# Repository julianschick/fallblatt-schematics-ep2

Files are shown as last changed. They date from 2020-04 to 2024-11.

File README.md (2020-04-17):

# Fallblattanzeiger der S-Bahn-Berlin

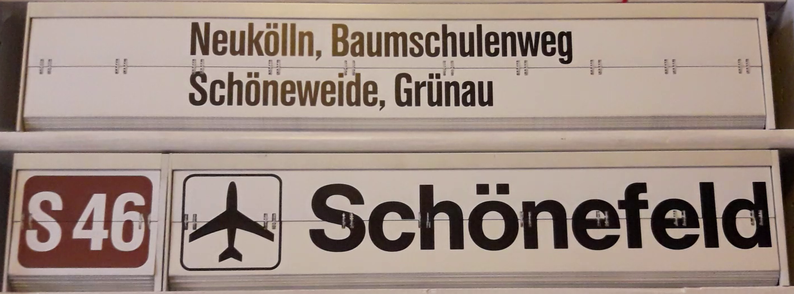
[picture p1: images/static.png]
Ansicht des Anzeigers


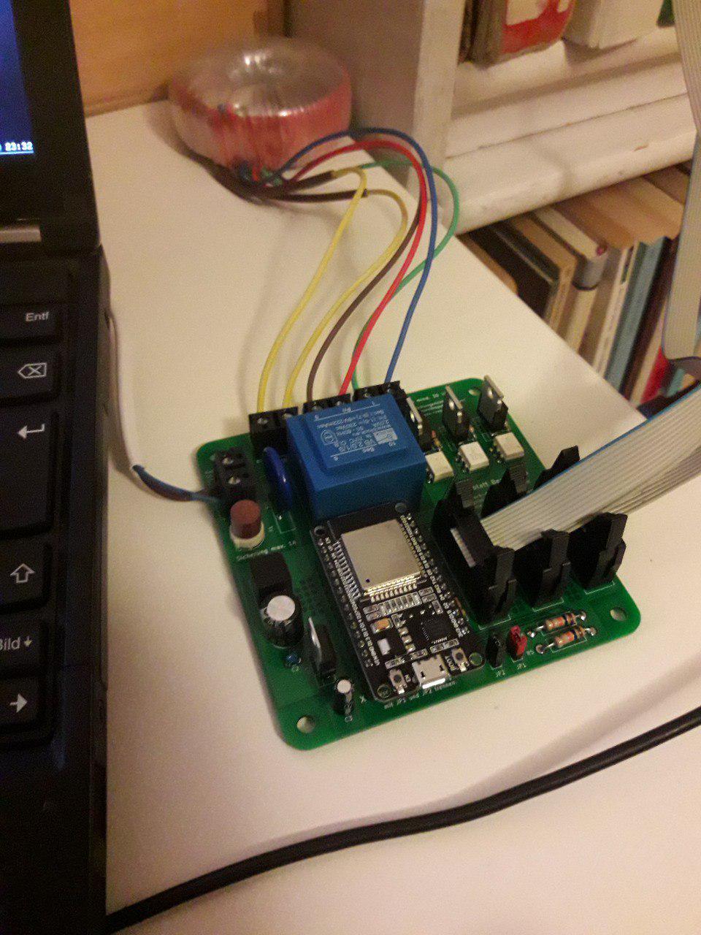
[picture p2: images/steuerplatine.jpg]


Platine zur Ansteuerung von 3 Fallblattmodulen (typischerweise Linie, Fahrtziel und Laufweg) mit einem ESP32-Development-Board. Gedacht für Module der *Epoche 2* (siehe [Wikipedia](https://de.wikipedia.org/wiki/Fallblattanzeige)) und ein Eingriff in die Platine der Module ist erforderlich. Der Synchronmotor wird nicht über die Transistorschaltung auf der Platine des Fallblattmoduls gesteuert. Vielmehr wird die Platine so überbrückt, dass der Microcontroller direkten Zugriff auf die Hall-Sensoren hat und über einen eigenen Triac den Synchronmotor direkt steuert.

Zur Stromversorgung wird die Platine an 230 V Netzspannung angeschlossen. Ein großer Trafo, der nicht auf der Platine verbaut wird, sondern über Schraubklemmen angeschlossen werden kann, spannt auf 48V AC herunter. Damit werden die Synchronmotoren der Module betrieben. Ein weiterer Trafo, der auf der Platine montiert wird, spannt auf 9V AC herunter, die gleichgerichtet und mit einem Linearregler auf Logik-Betriebsspannung 3,3V gebracht werden.

## Modifikationen an der Platine des Fallblattmoduls

Der unveränderte Schaltplan der Platine ist als [KiCad-Schaltplan](images/schaltplan-modul/schaltplan-modul.sch) und [PDF](images/schaltplan-modul.pdf) im Repo abgelegt. Soweit möglich, sind Typenbezeichnung der Bauteile mit angegeben, diese sind allerdings mit Google heute nur schwer zu deuten.

Ähnlich wie bei den modernen Varianten (siehe auch [fallblatt-schematics-ep3](https://github.com/julianschick/fallblatt-schematics-ep3)) der Fallblattmodule sind zwei Sensoren verbaut: Ein Sensor, der jedes fallende Blatt zählt (Flap) und einen, der ein bestimmtes Blatt als Nullstellung markiert (Home). Im Gegensatz zu den moderneren Exemplaren sind das allerdings keine Photodioden sondern Hall-Sensoren, an denen ein Magnet vorbeistreicht. Wenn kein Magnet in der Nähe ist, liegt auf dem Ausgang des Sensors VCC an, kommt der Magnet vorbei, so wird der Ausgang sehr sauber (ohne Gewackel) auf GND gezogen. Im Betrieb mit dem Mikrocontroller habe ich allerdings festgestellt, dass die Flap-Sensoren einerseits gerne etwas zu früh triggern, sodass das Blatt noch klemmt, und andererseits beim erneuten Anlaufen manchmal durch die Induktion des in Bewegung gesetzten Magneten noch einmal kurz getriggert werden. Gelöst habe ich beide Probleme auf Softwareseite durch etwas längeres Weiterlaufen und durch Ignorieren des Flap-Sensors direkt nach dem Anlaufen.

Die folgenden Pläne und Bilder zeigen die notwendigen Modifikationen. Einmal wird Pin 5 des Anschlusssteckers von Pin 10 des Anschlusssteckers getrennt, indem ein Widerstand und eine Diode entfernt werden. Außerdem wird Pin 10 direkt mit dem Flap-Hall-Sensor verbunden, durch setzen einer Brücke auf der Platine, wo schon zwei vorbereitete Pads nebeneinander liegen (violette Brücke). Zuletzt wird der Triac entfernt und überbrückt (blaue Brücke).

**Schaltplan mit Modifikationen**

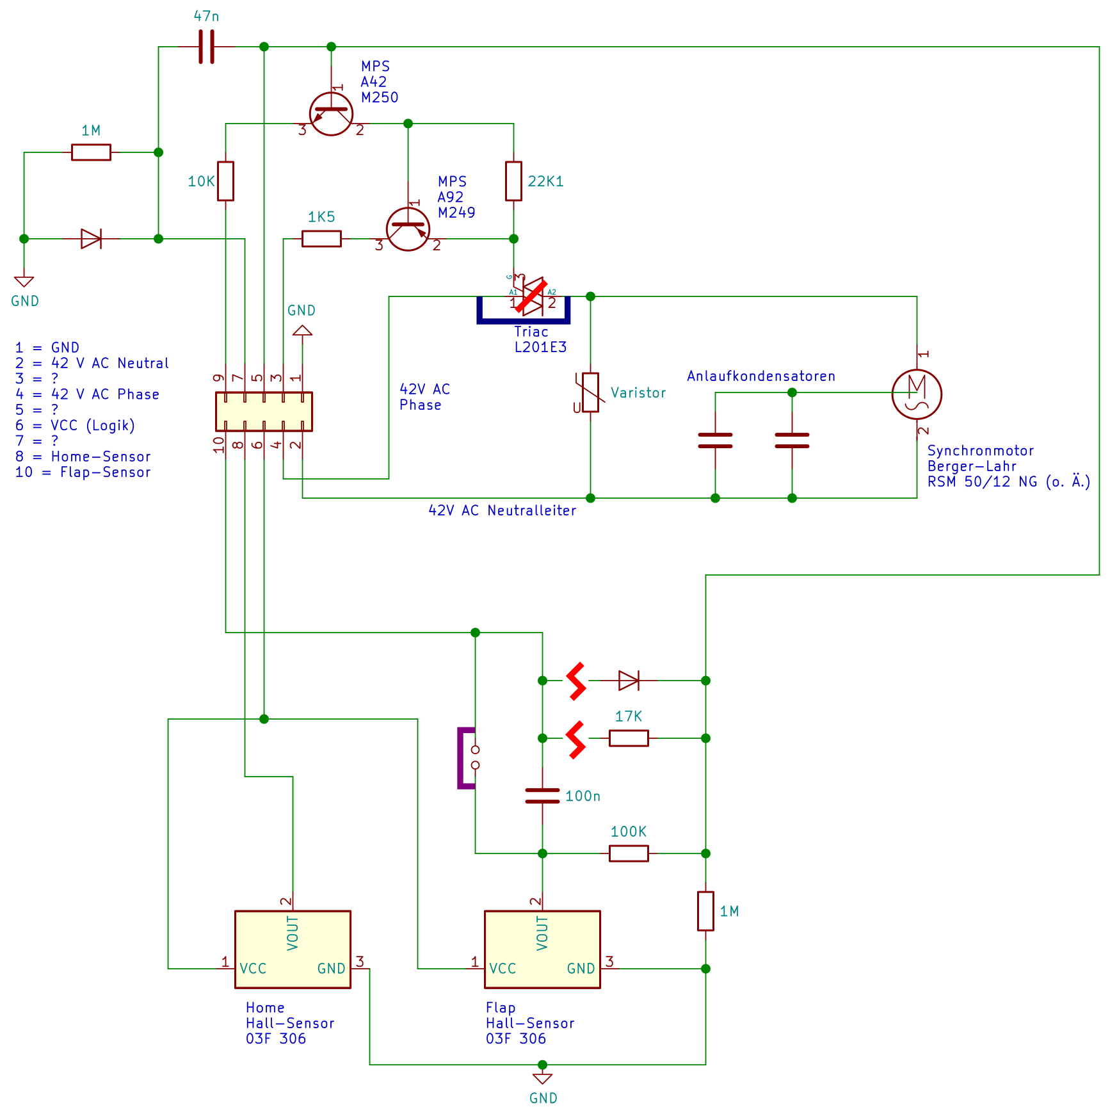
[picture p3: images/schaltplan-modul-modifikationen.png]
Schaltplan mit Modifikationen


Dieses Bild auch als [PDF](images/schaltplan-modul-modifikationen.pdf) und [SVG](images/schaltplan-modul-modifikationen.svg).

**Modifikationen an der Platine** (blaue und violette Brücke, entfernte Teile)

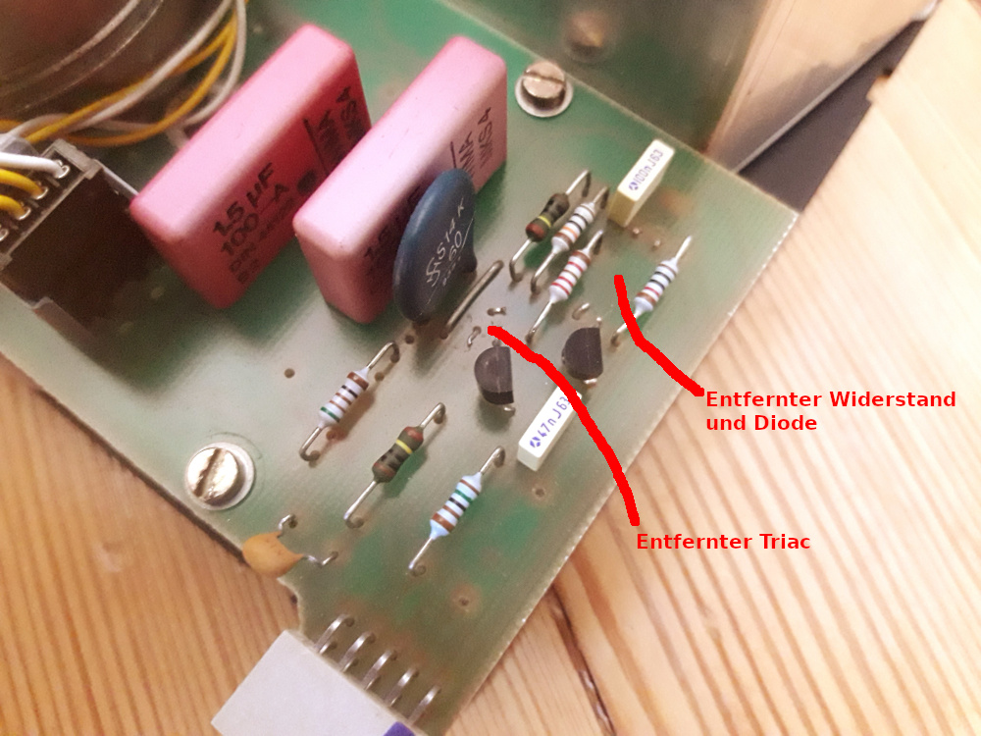
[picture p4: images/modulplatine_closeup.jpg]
Modifikationen an der Platine
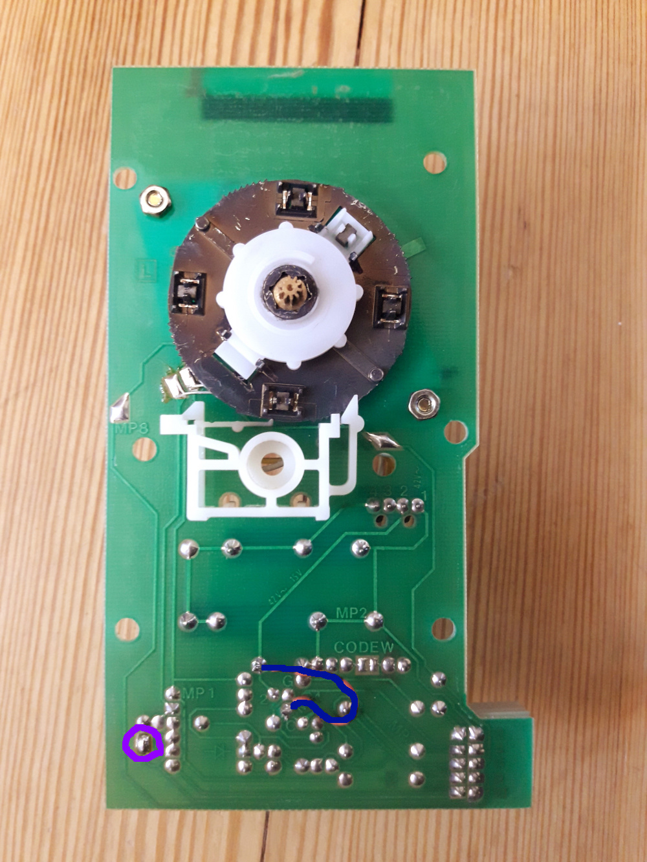
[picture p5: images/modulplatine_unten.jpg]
Modifikationen an der Platine
 

**Gesamte Platine des Fallblattmoduls / Synchronmotor**

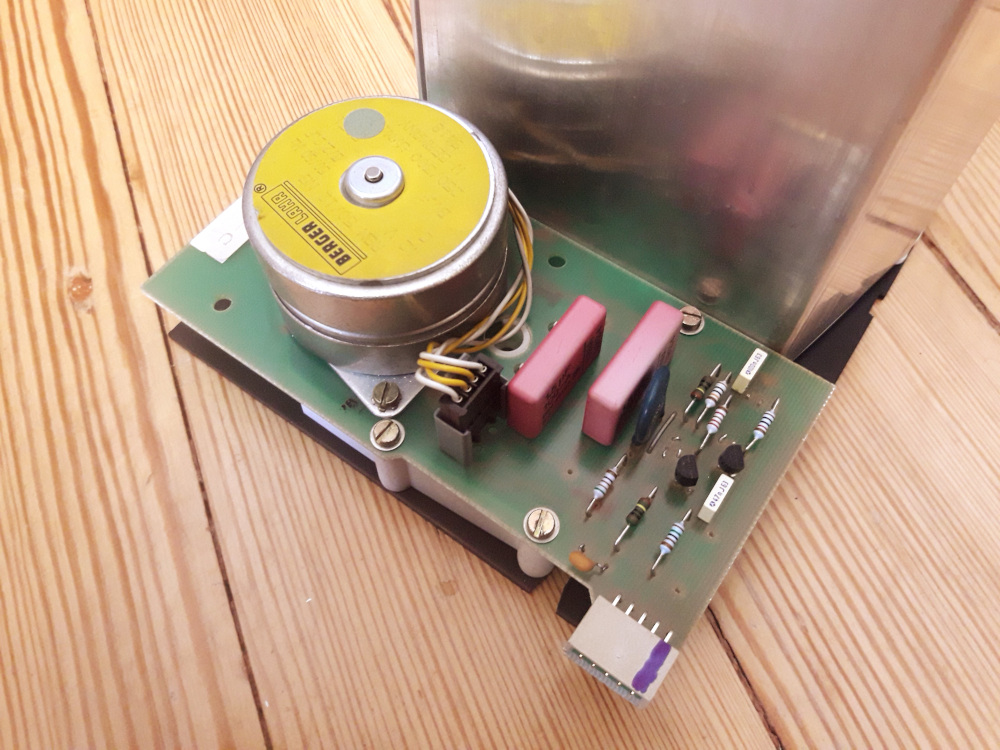
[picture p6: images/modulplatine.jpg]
Modulplatine
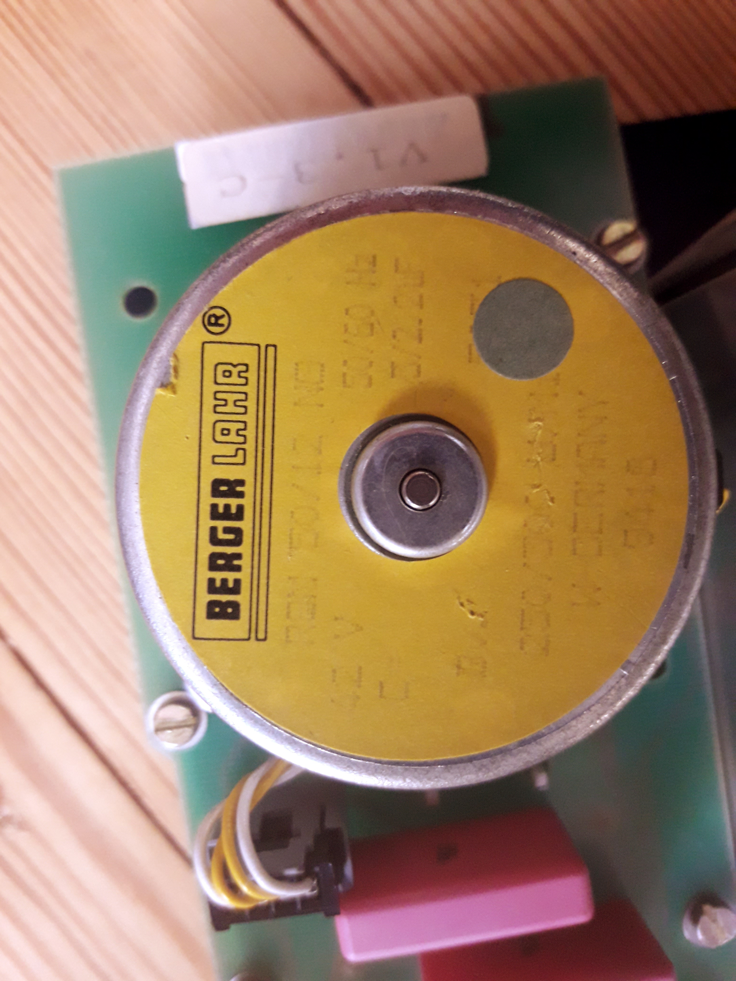
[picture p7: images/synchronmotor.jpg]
Synchronmotor
 

**Polbelegung des Anschlusses**

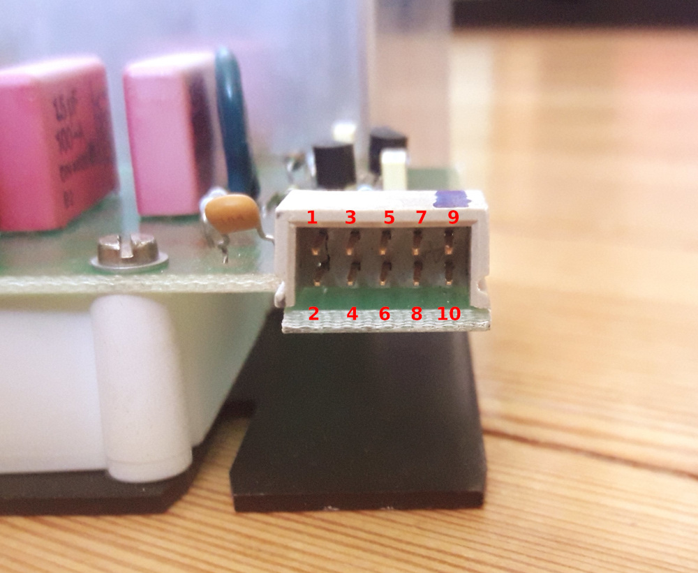
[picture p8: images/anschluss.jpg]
Polbelegung des Anschlusses


## Teileliste

* ESP32-Development-Board (es gibt 2 Varianten bei eBay, für diese Platine wird die üblichere mit 15 Pins je Reihe und GND/VCC  nebeneinander, nicht auf gegenüberliegenden Pins benötigt; diese wird oft unter dem Namen _DEVKITV1_ oder _NodeMCU_ verkauft). Das folgende Pinout ist das korrekte:

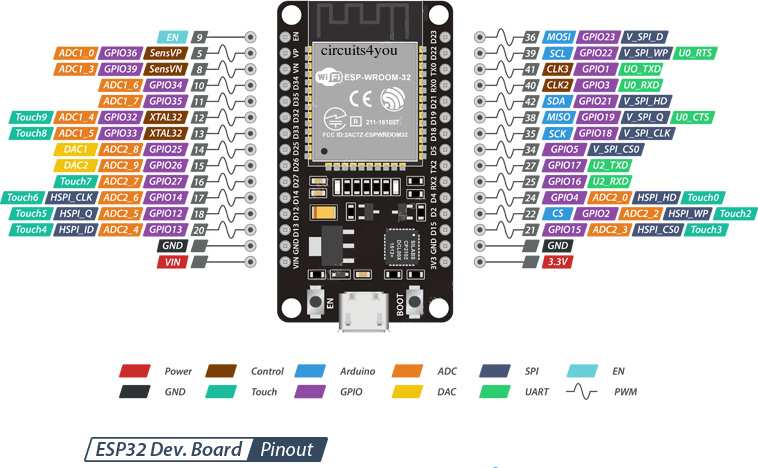
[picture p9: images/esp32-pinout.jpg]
ESP32-Pinout


* Netztrafo 48V (eigentlich 42V) mit Wumms, mind. 200mA pro Modul, der Synchronmotor zieht so viel. Zum Beispiel [der hier](https://www.voelkner.de/products/1011896/TRU-Components-TC-RKT30-2X24-Ringkerntransformator-1-x-230V-2-x-24V-30-VA-625mA.html)
* [Transformator 9V _Block VB 2,0/1/9_](https://www.reichelt.de/printtrafo-2-va-9-v-222-ma-rm-20-mm-ei-30-15-5-109-p27328.html)
* Rundsicherung 1A mit Halter Littelfuse, RM 5mm
* Varistor, mind. 300V, RM 10mm
* [Brückengleichrichter Rund, Wechselstrompins gegenüber, RM 5mm](https://www.reichelt.de/brueckengleichrichter-100-v-1-5-a-b70c1500rund-p181713.html)
* 4 x Schraubklemme 2-polig RM 7,5mm
* [Spannungsregler 3,3V Formfaktor TO-220 _STM LD1117 V33C_](https://www.reichelt.de/ldo-regler-fest-3-3-v-to-220-ld1117-v33c-p200891.html?)
* 3 x Optotriac (Triac mit Optokoppler) MOC3041M, Formfaktor DIP-6
* 3 x Leistungstriac BT136-600, Formfaktor TO-220
* Elektrolytkondensator 470u, RM 5mm
* Elektrolytkondensator 10u, RM 2mm
* Kondensator 100n, RM 2,5mm
* 6 x Widerstand 10K, RM 15mm
* 3 x Widerstand 220, RM 10mm
* 3 x Widerstand 330, RM 10mm
* 2 x Jumpersteckplatz und 2 x Pinheader Female für das ESP32-Board
* 3 x Anschlüsse für die Fallblattmodule (2 x 5 Pole), RM 2,54mm

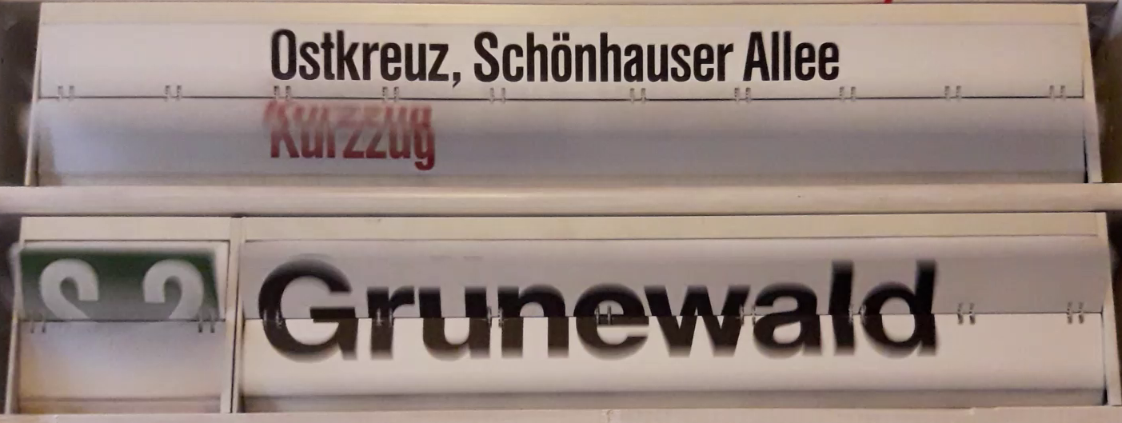
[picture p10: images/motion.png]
In Bewegung


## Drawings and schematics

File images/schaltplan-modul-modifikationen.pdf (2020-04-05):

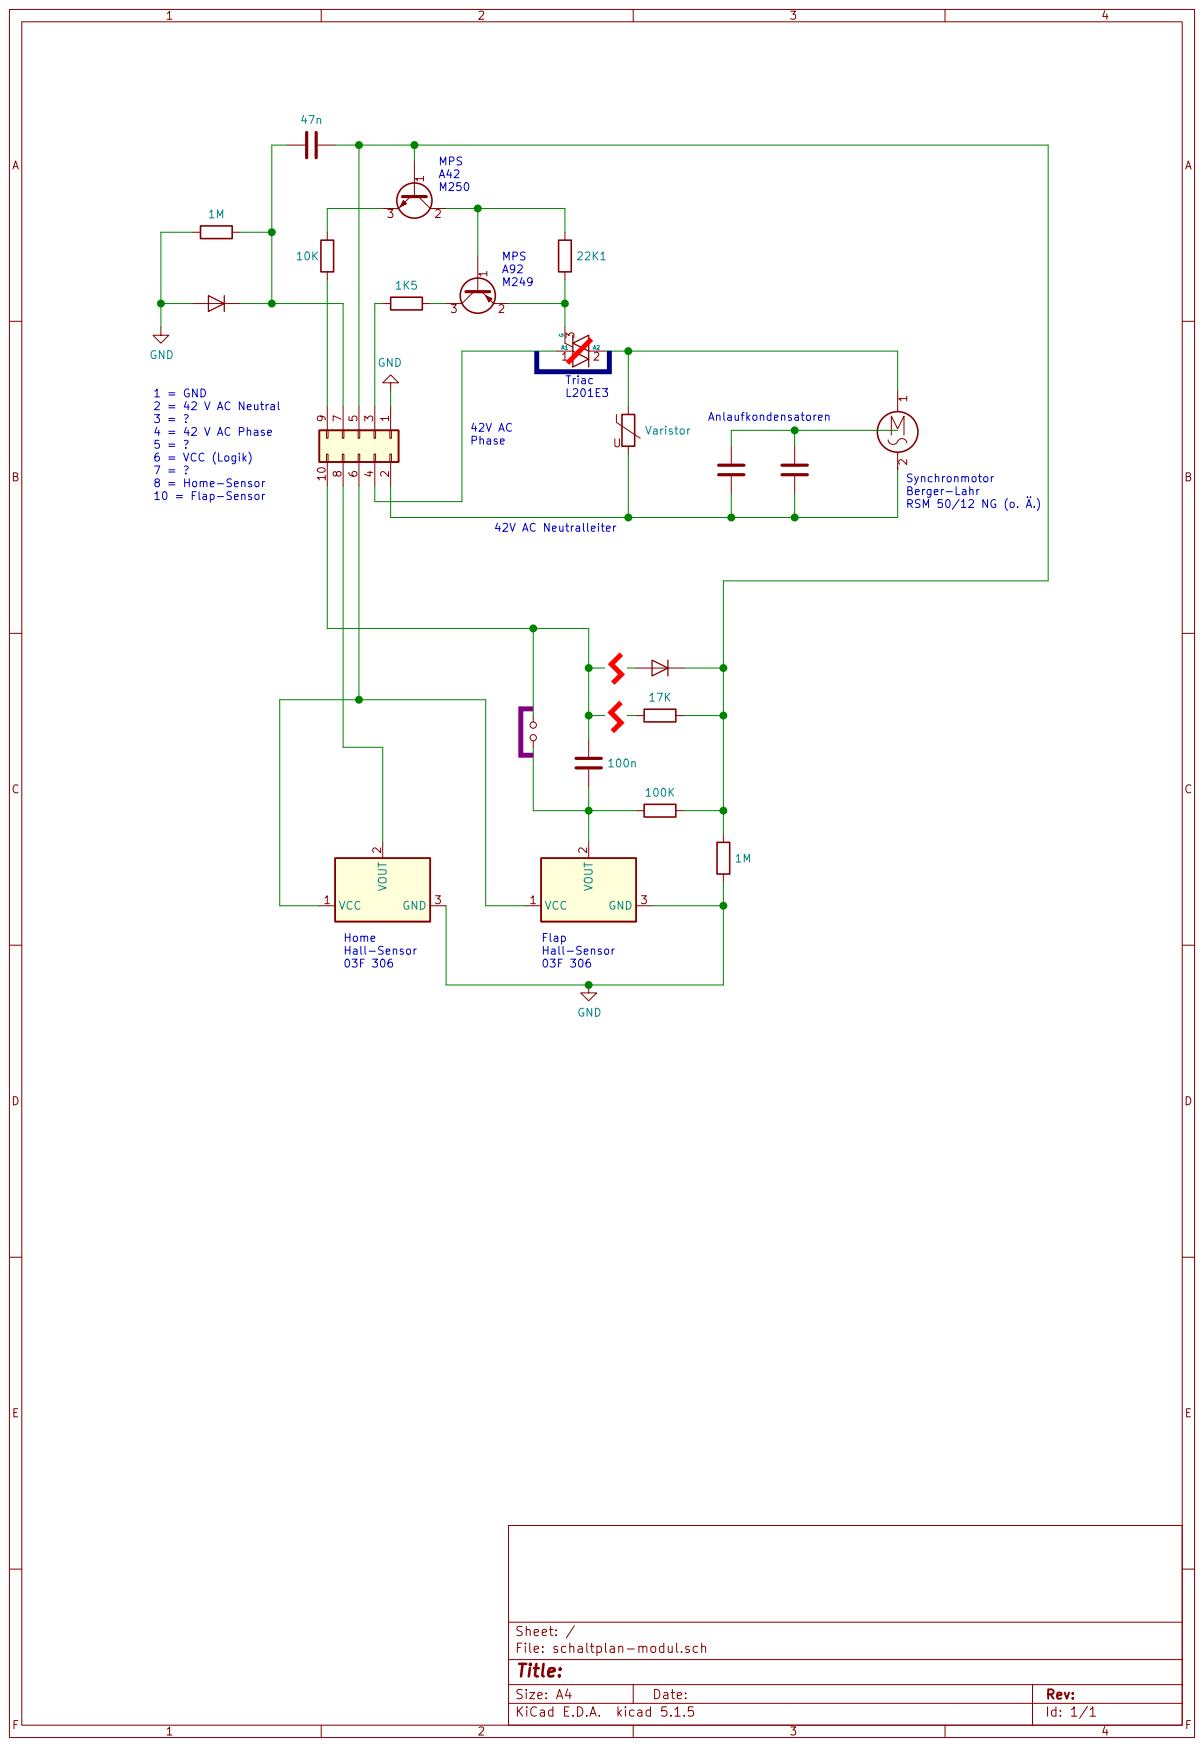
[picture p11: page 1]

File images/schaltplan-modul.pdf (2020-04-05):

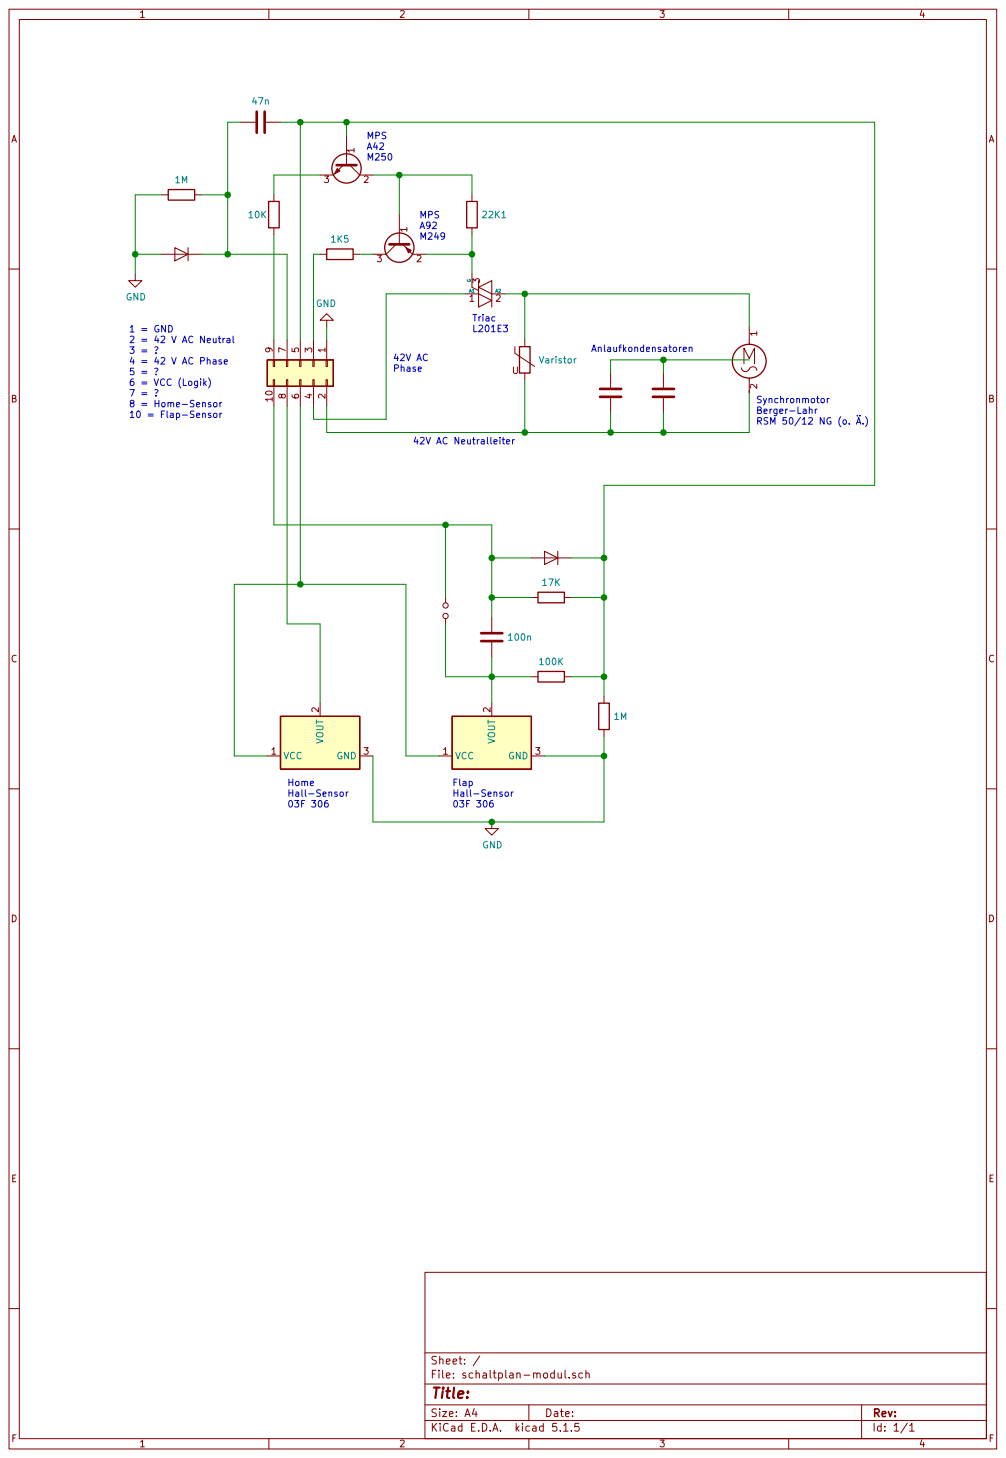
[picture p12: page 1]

File: schaltplan-modul.sch Sheet: /

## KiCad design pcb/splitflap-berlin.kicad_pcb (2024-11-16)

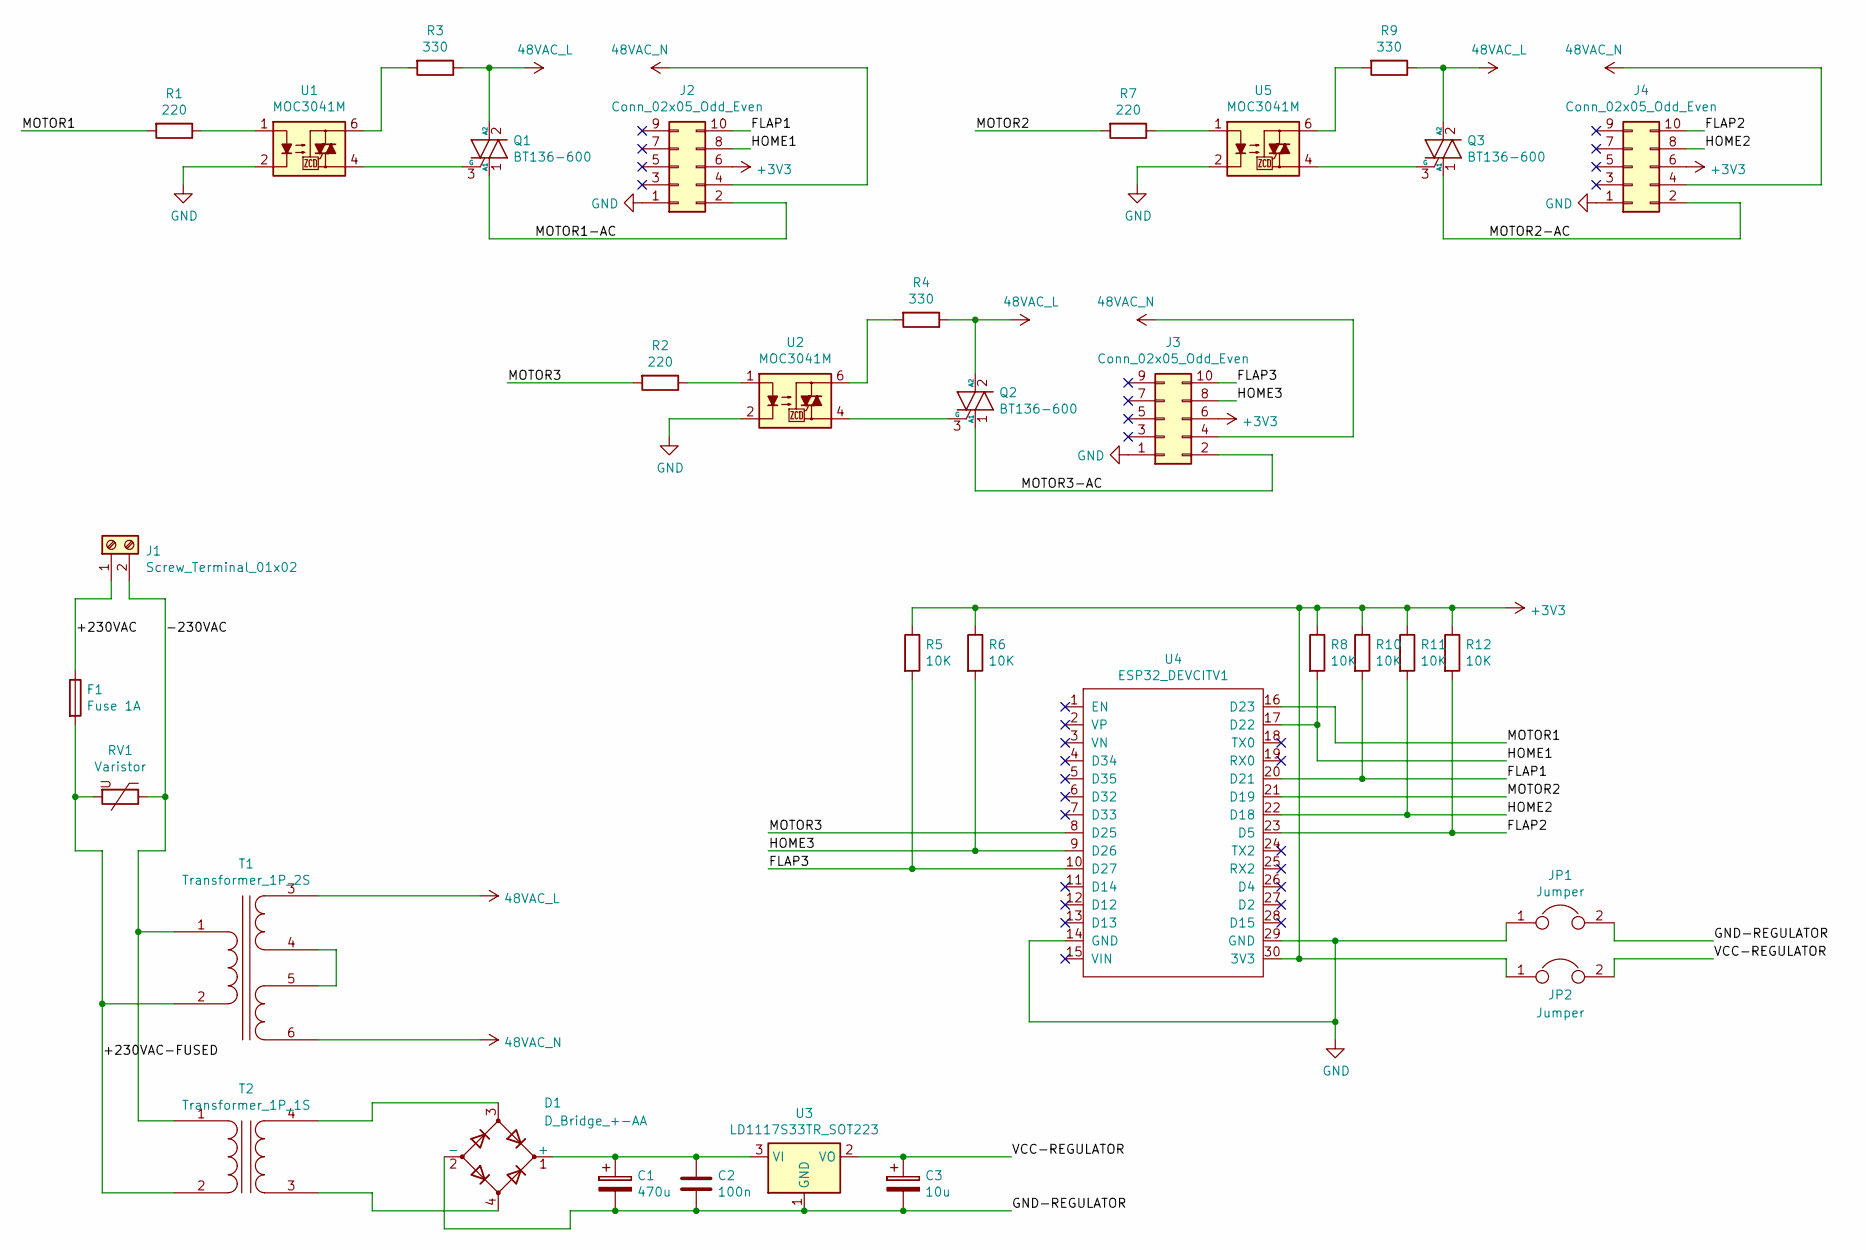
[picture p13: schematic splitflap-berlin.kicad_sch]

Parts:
C1: 470u; CP_Radial_D10.0mm_P5.00mm
C2: 100n; C_Disc_D3.0mm_W1.6mm_P2.50mm
C3: 10u; CP_Radial_D4.0mm_P2.00mm
D1: D_Bridge_+-AA; Diode_Bridge_9.5x9.5x10mm_P5.08mm
F1: Fuse 1A; Fuseholder_TR5_Littelfuse_No560_No460
J1: Screw_Terminal_01x02; TerminalBlock_MetzConnect_Type175_RT02702HBLC_1x02_P7.50mm_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
J2, J3, J4: Conn_02x05_Odd_Even; TE_CON_5499922-1_BIGGERHULL
JP1, JP2: Jumper; PinHeader_1x02_P2.54mm_Vertical
Q1, Q2, Q3: BT136-600; TO-220-3_Vertical
R1, R2, R7: 220; R_Axial_DIN0207_L6.3mm_D2.5mm_P10.16mm_Horizontal
R3, R4, R9: 330; R_Axial_DIN0207_L6.3mm_D2.5mm_P10.16mm_Horizontal
R5, R6, R8, R10, R11, R12: 10K; R_Axial_DIN0411_L9.9mm_D3.6mm_P15.24mm_Horizontal
RV1: Varistor; RV_Disc_D21.5mm_W4.3mm_P10mm
T1: Transformer_1P_2S; Transformer_Ext_1P_2S
T2: Transformer_1P_1S; Block_VB_2.0_1_9
U1, U2, U5: MOC3041M; DIP-6_W7.62mm
U3: LD1117S33TR_SOT223; TO-220-3_Vertical
U4: ESP32_DEVCITV1; ESP32_DEVKITV1_16

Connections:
48VAC_L: Q1.2 (A2), Q2.2 (A2), Q3.2 (A2), R3.1, R4.1, R9.1, T1.3 (SA)
48VAC_N: J2.4, J3.4, J4.4, T1.6 (SD)
+3V3: J2.6, J3.6, J4.6, JP2.1, R5.1, R6.1, R8.1, R10.1, R11.1, R12.1, U4.30 (3V3)
/+230VAC: F1.1, J1.1
/+230VAC-FUSED: F1.2, RV1.2, T1.2 (AB), T2.2 (AB)
/-230VAC: J1.2, RV1.1, T1.1 (AA), T2.1 (AA)
/FLAP1: J2.10, R10.2, U4.20 (D21)
/FLAP2: J4.10, R12.2, U4.23 (D5)
/FLAP3: J3.10, R5.2, U4.10 (D27)
/GND-REGULATOR: C1.2, C2.2, C3.2, D1.2 (-), JP1.2, U3.1 (GND)
/HOME1: J2.8, R8.2, U4.17 (D22)
/HOME2: J4.8, R11.2, U4.22 (D18)
/HOME3: J3.8, R6.2, U4.9 (D26)
/MOTOR1: R1.2, U4.16 (D23)
/MOTOR1-AC: J2.2, Q1.1 (A1)
/MOTOR2: R7.2, U4.21 (D19)
/MOTOR2-AC: J4.2, Q3.1 (A1)
/MOTOR3: R2.2, U4.8 (D25)
/MOTOR3-AC: J3.2, Q2.1 (A1)
/VCC-REGULATOR: C3.1, JP2.2, U3.2 (VO)
GND: J2.1, J3.1, J4.1, JP1.1, U1.2, U2.2, U4.14 (GND), U4.29 (GND), U5.2
unnamed: C1.1, C2.1, D1.1 (+), U3.3 (VI)
unnamed: D1.3, T2.4 (SB)
unnamed: D1.4, T2.3 (SA)
unnamed: Q1.3 (G), U1.4
unnamed: Q2.3 (G), U2.4
unnamed: Q3.3 (G), U5.4
unnamed: R1.1, U1.1
unnamed: R2.1, U2.1
unnamed: R3.2, U1.6
unnamed: R4.2, U2.6
unnamed: R7.1, U5.1
unnamed: R9.2, U5.6
unnamed: T1.4 (SB), T1.5 (SC)

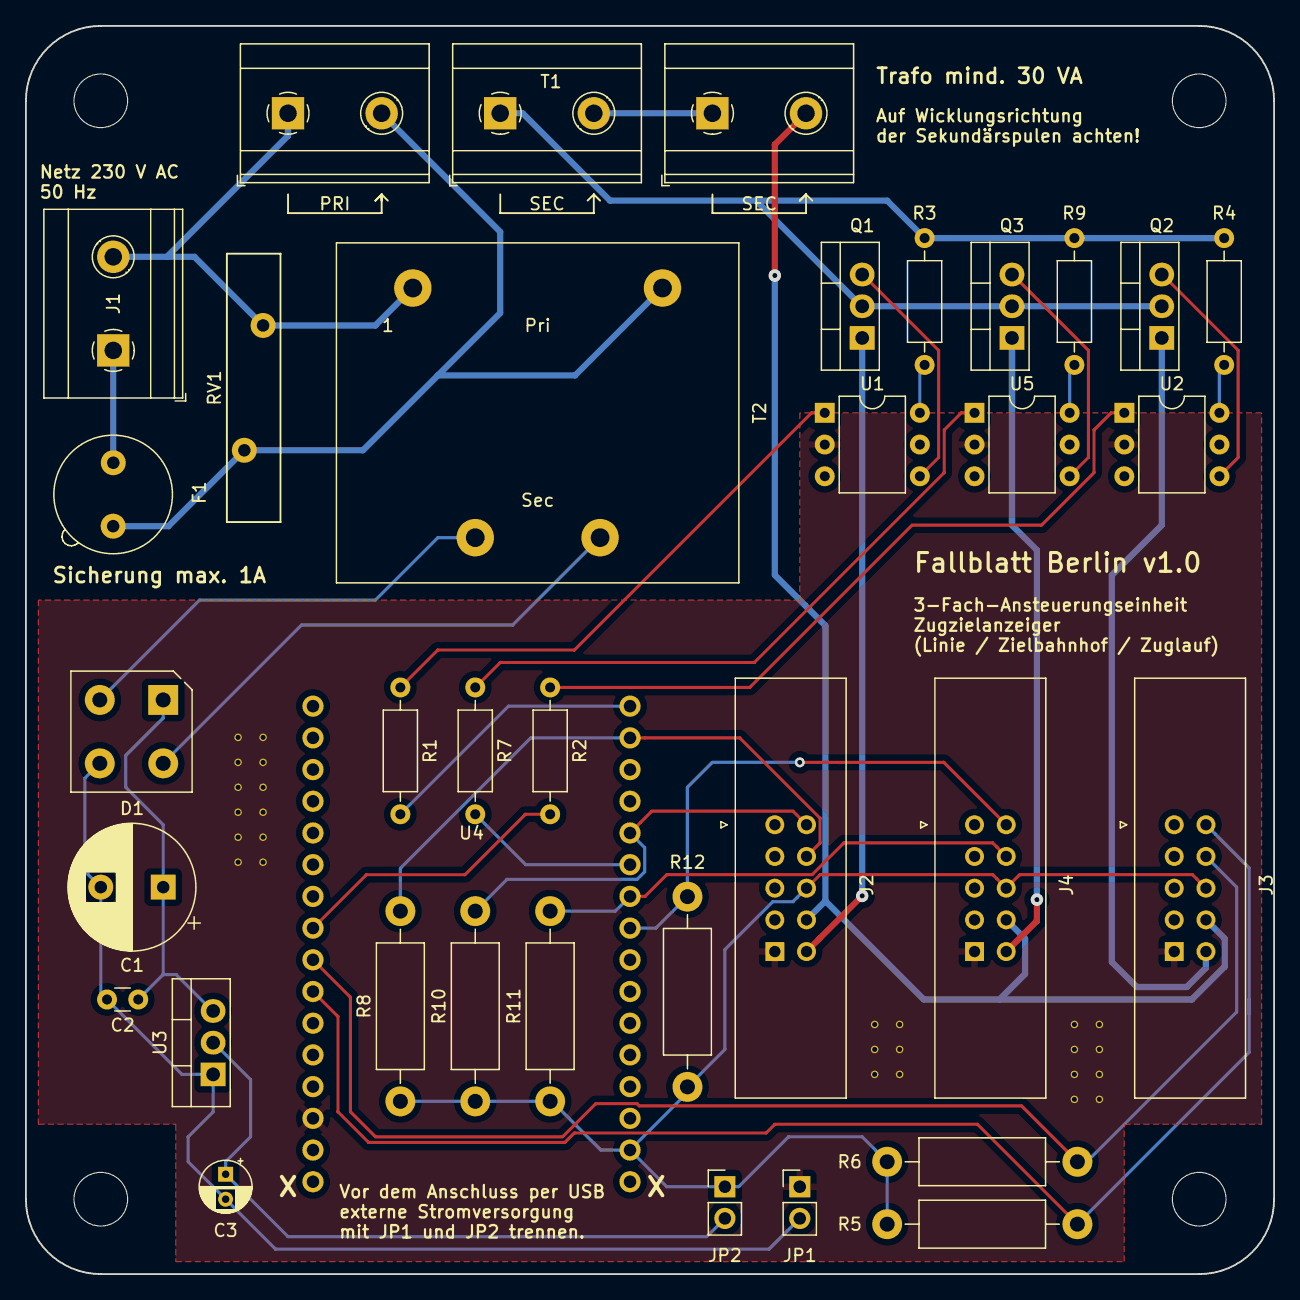
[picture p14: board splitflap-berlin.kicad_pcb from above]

Board: 2 copper layers, 100.0 x 100.0 mm, 34 parts (0 on the bottom side), 34 nets.

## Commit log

2020-04-05 images added
    [schaltplan-modul.sch]
2024-11-16 opened with newer kicad-version
    [splitflap-berlin.kicad_pcb, splitflap-berlin.kicad_sch]
